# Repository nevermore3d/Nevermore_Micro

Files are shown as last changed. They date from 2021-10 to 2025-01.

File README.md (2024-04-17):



# Nevermore Activated Carbon Filters - Micro Edition

<div align="center">Nevermore Micro V5 Duo (dual fan)</div>

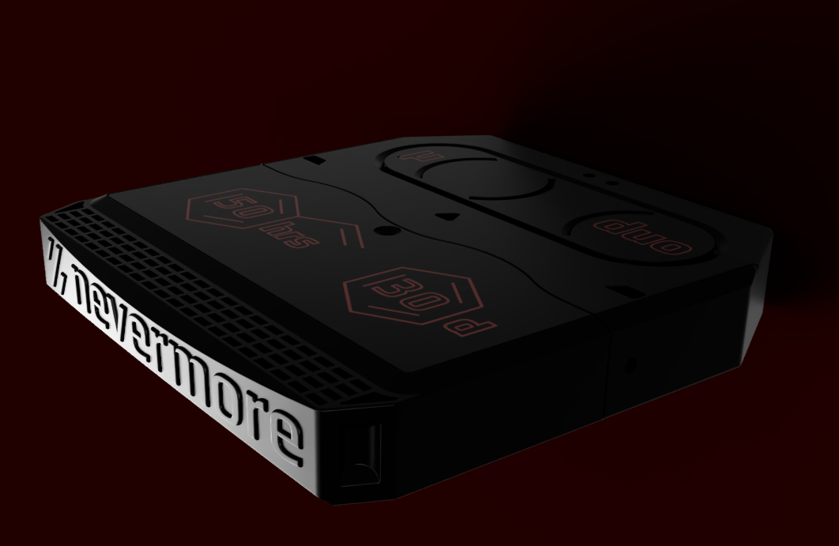
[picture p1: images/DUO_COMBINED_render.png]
Nevermore Activated Carbon Filter Micro V5 Duo


<div align="center">Nevermore Micro V4 (single fan)</div>

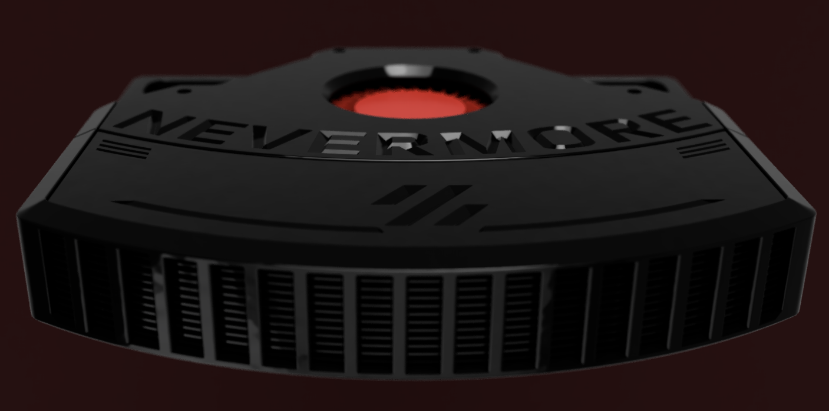
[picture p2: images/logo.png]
Nevermore Activated Carbon Filter Micro V4


Originally intended as a carbon fume filter for Voron V2, it has found its way into a multitude of other machines. Let yours be the next! Bad smells or fumes, or complaints thereof, should not keep you from being a maker!

- [Nevermore Activated Carbon Filters - Micro Edition](#nevermore-activated-carbon-filters---micro-edition)
- [About The Nevermore Micro](#about-the-nevermore-micro)
  - [Why The Nevermore?](#why-the-nevermore)
  - [Nevermore Background](#nevermore-background)
  - [Nevermore V4, First Release](#nevermore-v4-first-release)
  - [Nevermore V5 Duo](#nevermore-v5-duo)
- [FAQs](#faqs)
  - [What are differences between V4 and V5 Duo?](#what-are-differences-between-v4-and-v5-duo)
  - [Why use a single fan version, if dual is better?](#why-use-a-single-fan-version-if-dual-is-better)
  - [What other changes does V5 bring?](#what-other-changes-does-v5-bring)
  - [What fans should I use?](#what-fans-should-i-use)
  - [How do I make a suggestion/report a bug/find out more?](#how-do-i-make-a-suggestionreport-a-bugfind-out-more)
- [Getting Started](#getting-started)
  - [SOURCING THE PROPER ACID-FREE CARBON](#sourcing-the-proper-acid-free-carbon)
  - [NEVERMORE 3D PRINTER CARBON](#nevermore-3d-printer-carbon)
  - [BOM (V5)](#bom-v5)
  - [BOM (V4)](#bom-v4)
  - [Assembly](#assembly)
    - [Instructions for V5](#instructions-for-v5)
    - [Instructions for V4](#instructions-for-v4)
  - [Final Thoughts on Usage](#final-thoughts-on-usage)
- [Credits](#credits)
  - [Contributing](#contributing)
  - [License](#license)
  - [Contact](#contact)
  - [Acknowledgements](#acknowledgements)
  - [Special Thanks](#special-thanks)

# About The Nevermore Micro

[VOCs (Volatile Organic Compounds)](https://en.wikipedia.org/wiki/Volatile_organic_compound) are common in daily life but VOCs generated from 3D printing are known to cause severe health issues and even cause cancer in some cases.

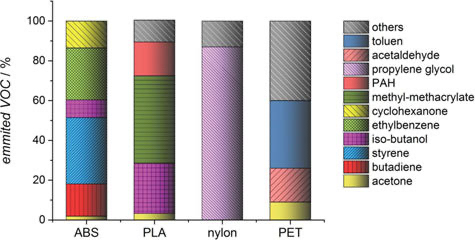
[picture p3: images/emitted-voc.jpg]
Emitted VOCs


A study from 2013 of [ultrafine particle emissions from desktop 3D printers (2013)](https://www.sciencedirect.com/science/article/pii/S1352231013005086) is a good start to understand the importance of your filament choices and the printer's environment.

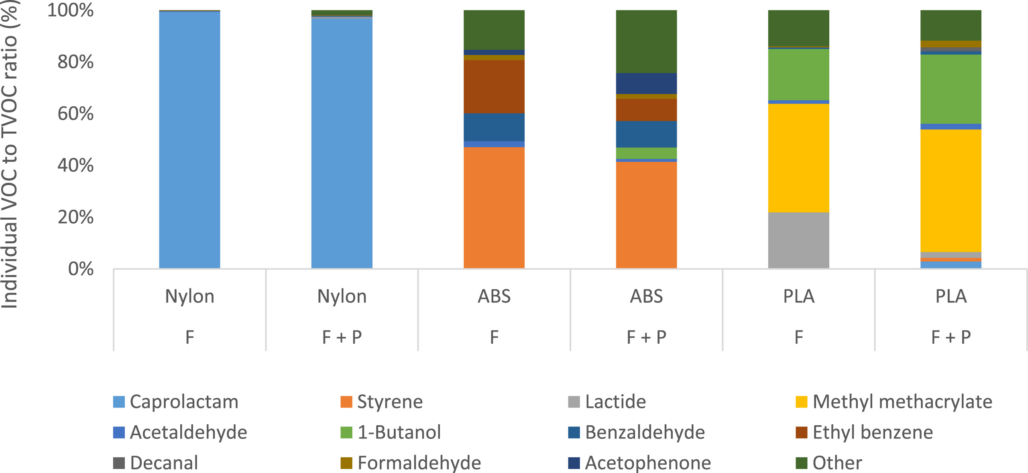
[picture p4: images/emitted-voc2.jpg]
Characterization of volatile organic compound emissions from consumer level material extrusion 3D printers (2019)

_(credit: [Characterization of volatile organic compound emissions from consumer level material extrusion 3D printers (2019)](https://www.sciencedirect.com/science/article/pii/S0360132319304196))_

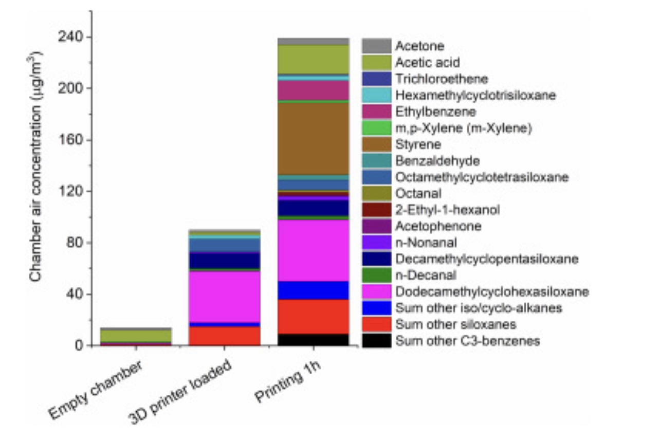
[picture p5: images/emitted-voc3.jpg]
Characterization of particulate and gaseous pollutants emitted during operation of a desktop 3D printer (2019)

_(credit: [Characterization of particulate and gaseous pollutants emitted during operation of a desktop 3D printer (2019)](https://www.sciencedirect.com/science/article/pii/S0160412018323663))_

## Why The Nevermore?

At the end of the day, a fresh single-pass filtered exhaust (at brand new) has perhaps 70% VOC removal efficiency while still exhausting 30% of the nasty. A worn-in 50% efficiency recirculation filter achieving four passes would still remove 94% of the bad stuff. Or 99% at six passes!

The number of passes you get all depends on how well you can seal your build chamber.

Some will have a hard time achieving a good chamber seal, which creates the biggest drawback of recirculation filters - _they're air flow neutral_. Meaning, as nothing pulls air into the chamber, air can diffuse freely to the outside through any remaining gaps. And that air could be _zero-per-cent_ cleaned...

If you plan on using only a Nevermore - be sure to seal your chamber as good as possible to prevent diffusing.

## Nevermore Background

There are many options for 3d printing air filters. Here’s a short list, and why I eventually settled on creating Nevermore:

**1. Home air purifiers**

**PRO:** Plug and play! High air flow (mostly). Will filter most particles a 3d printer produces.

**CON:** ABS headaches are not from particles, but Volatile Organic Compounds (VOCs), that are two orders of magnitude smaller than any particles a HEPA or ULPA could trap - they’re essentially gasses.

While home purifiers typically also contains carbon filtration and/or photocatlytic UV filtration stages, they will still not be suitable for 3d printing. Why? Efficient carbon adsorption in sufficient amount and stages is an absolute airflow killer, so most purifiers contain only a thin layer of carbon mesh/pellets that will be fully adsorbed within days or weeks at full power. And even if the filter is not used, contact with air saturates the carbon in 1-2 months. Yet they’re advertised as lasting for 6 months – that's only true for the HEPA component, not the VOC adsorbant carbon we're after.

And replacement filters typically run 20-60 USD a pop. Quite a lot for changing every few weeks when the carbon component depletes.

UV photocatalyst activity can last though; however, breakdown is slow and inefficient with voc halflives of several hours. The TiO2 layer reacting to the UV will also easily get irreversibly blocked by silicates (of which there are a lot in peoples homes, in everything from sink and bathroom sealants to plaster walls). And breakdown will many times be incomplete. Styrene passing a PCO filter might get turned to even more dangerous benzene, for instance.

**2. Carbon/HEPA filter combinations like the Zortrax M Series HEPA Filters**

Same as above. The HEPA component will keep working, but the carbon is just a few pebbles per hex. It could provide partial VOC clearance when fresh, but will quickly deplete with air flow. Then you need to replace it for 36 USD after a week of printing.

**3. Wet scrubber**

Awesome for both particles and VOCs, but its an industrial solution with any smaller home versions plagued by loud noise, water leakage and mechanical issues. It's not a solution for the masses.

**So, how about Nevermore?**

Well, the carbon in those filters mentioned above, costing a lot for little duration is actually dirt cheap. Whereas you get 20 grams for 36 USD with a zortax filter, **you can get 5000 grams for 36 USD in bulk**.

And with an enclosed chamber, you don't need the air flow of a room-size air purifier. Even a 350mm V2 Voron only holds about 5cf, meaning even a partial flow from a 5015 fan of 0.5-2cfm is enough to filter the fumes efficiently at the source.

So what are we waiting for? We got lots of cheap carbon. We can replace it easily. We don't need high airflow to clean a small chamber. We deal with poor efficiency of one-pass carbon filters by multiplying the amount and recirculate the air.

Enter, _The Nevermore_.

## Nevermore V4, First Release

Nevermore V4 is a refinement of the V3. V4 adds a air guides, as the previous versions had the majority of air flow on just one side of the filter (most recent version has all supports removed yet again!). The cartridge lid also mounts a bit sturdier, and V4 now has separate base pieces for use with Vorons other than 2.4.

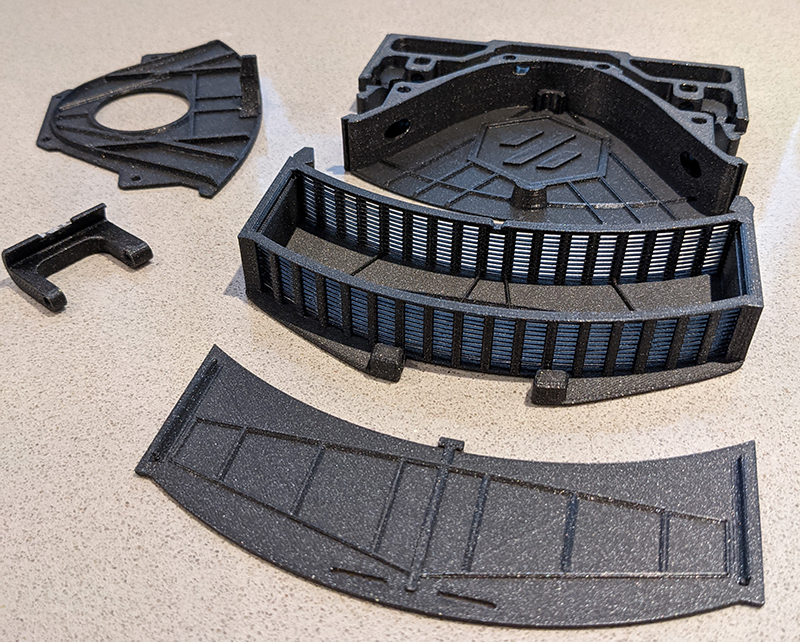
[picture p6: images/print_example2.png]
Nevermore Micro V2 Prototype


The V4 was the first official release of the Nevermore Micro to the public.

## Nevermore V5 Duo

Following the V4, the V5 Duo was released that changes the direction of air flow, better suited for when the Nevermore Micro would be placed flat on the bottom or top of the printer. Though there are other "outlet" options, like for the V1.8/Trident style that blows outwards and not up.

The V5 Duo also adds a 2nd additional 5015.

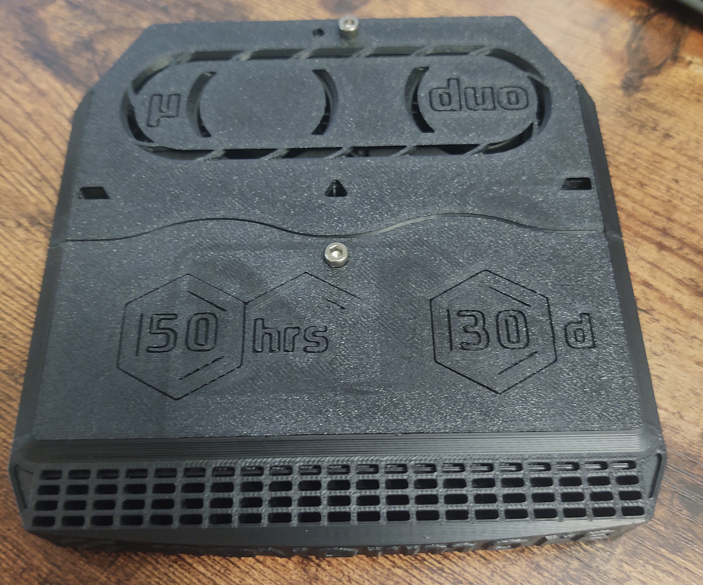
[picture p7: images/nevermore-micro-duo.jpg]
Nevermore Micro V5 Duo


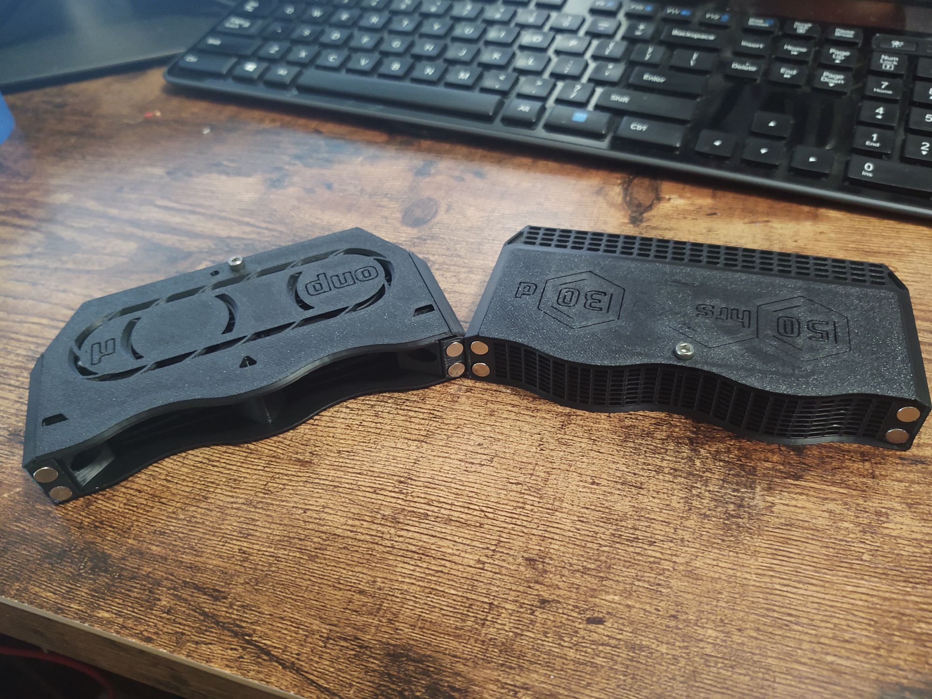
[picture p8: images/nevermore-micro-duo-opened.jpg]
Nevermore Micro V5 Duo


_(Nevermore V5 Duo. used with permission from Tightwad(JT)#6055)_

This repository hosts both versions, as they are the same in design and function.

# FAQs

## What are differences between V4 and V5 Duo?

The current NM Micro versions are V4 and V5 Duo.

V4 utilizes a single dissected 5015 fan that is glued in place to spread the airflow over the entire filter surface (something impossible to do with an intact scroll, which focuses the air too much). The intake is on the top, and exhausts out the front.

V5 Duo uses two blowers in parallel to achieve a more even spread of airflow while keeping the pressure-generating scrolls intact; however, it still needs some slight modifications to the scroll exhaust. The intake is on the top, and exhausts upwards.

## Why use a single fan version, if dual is better?

_Dual is not better._ The area per blower is halved, so what is gained in air flow is lost in increased restriction per blower. There should be some improvements though, from linear air flow and intact scroll.

Also, the V4 single fan version may be better suited for printers where the Micro has to be mounted vertically, like on the side of a Voron V0.

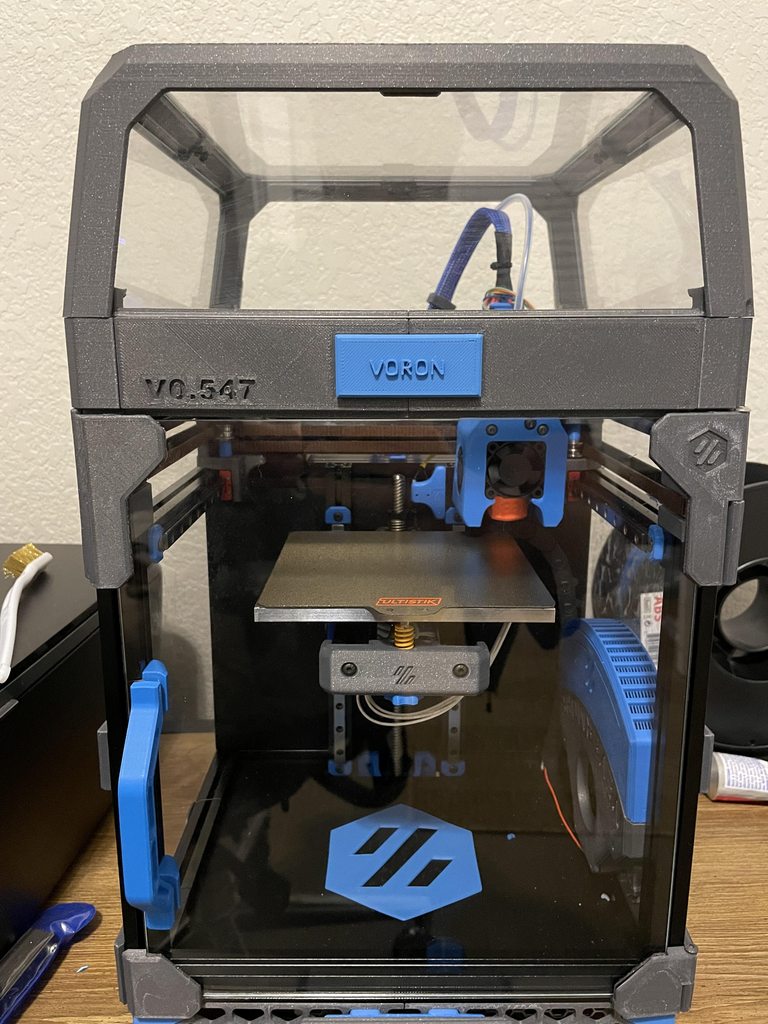
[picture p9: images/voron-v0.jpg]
Voron V0.1 with Nevermore V4


_(Voron V0.1 w/Nevermore V4. used with permission from DoubleT#0448)_

The single fan version of the V4 design in the Voron V0 above would draw the air from under the build plate, and exhaust it upwards, creating a circulation flow within the printer.

Air circulation is critical to filter as much of the VOCs within the build chamber as possible. Not only that, but it would help heat the chamber faster and achieve higher chamber temps.

However, on a Voron V2 or similar printer, the V5 Duo version would be better suited when placed under the bed as the upward exhaust venting creates a good circulation effect.



_(Voron V2 w/Nevermore V5. used with permission from Laserbeak43#2729)_

## What other changes does V5 bring?

- Exhausts air upwards
  - Better heat spread in the Voron V2 chamber
  - Less air leaks through Voron V2 split doors
- BOM 6x3 magnets are standard
- Blower fans are seated by bolts again, with less modifications needed

## What fans should I use?

Aim for any 5015 blower with a rating above 200Pa / 20mmH2O / 1 inH2O.

Since the fan (probably) cant be reused for other projects and will function in a high temp environment affecting its lifetime, go for budget. The Sunon Maglev MF50151VX (12V) / MF50152VX (24V) (high speed version, 6000 rpm) is good but unfortunately almost impossible to find as most are fakes. The GDStime 6000rpm Dual Ball bearing is another good option, but quality may vary. The Delta BFB0524HH is a gucci option, as is the special micro versions made for the papst rlf-35 which is an equally awesome and expensive fan. Any fan that works well for stealthburner should be a good option for nevermore micro as well.

See the BOM below for more details.

## How do I make a suggestion/report a bug/find out more?

- [The Nevermore Micro](https://github.com/nevermore3d/Nevermore_Micro)
  - [Report a Bug](https://github.com/nevermore3d/Nevermore_Micro/issues)
  - [Request a Feature](https://github.com/nevermore3d/Nevermore_Micro/issues)
- [Explore all Nevermore Activated Carbon Filters](https://github.com/nevermore3d)

# Getting Started

You're ready to build a Nevermore Micro? Cool!

> [!NOTE]  
> MADE FOR ABS/PC/PETG - USE A DECENTLY HEAT RESISTANT FILAMENT !!

> [!NOTE]  
>  Since you are committing to fan dissection, be aware a 5015 used for a NM Micro will most likely never find a different purpose!

## SOURCING THE PROPER ACID-FREE CARBON

**IMPORTANT!** Since first release the varying quality carbon out there has become increasingly evident. Users has both gotten bad carbon as well as outright dangerous stuff (in one case oxidizing most metal surfaces in a new voron in minutes. Be sure to vet your carbon supplier! You do not want your printer to look like this.

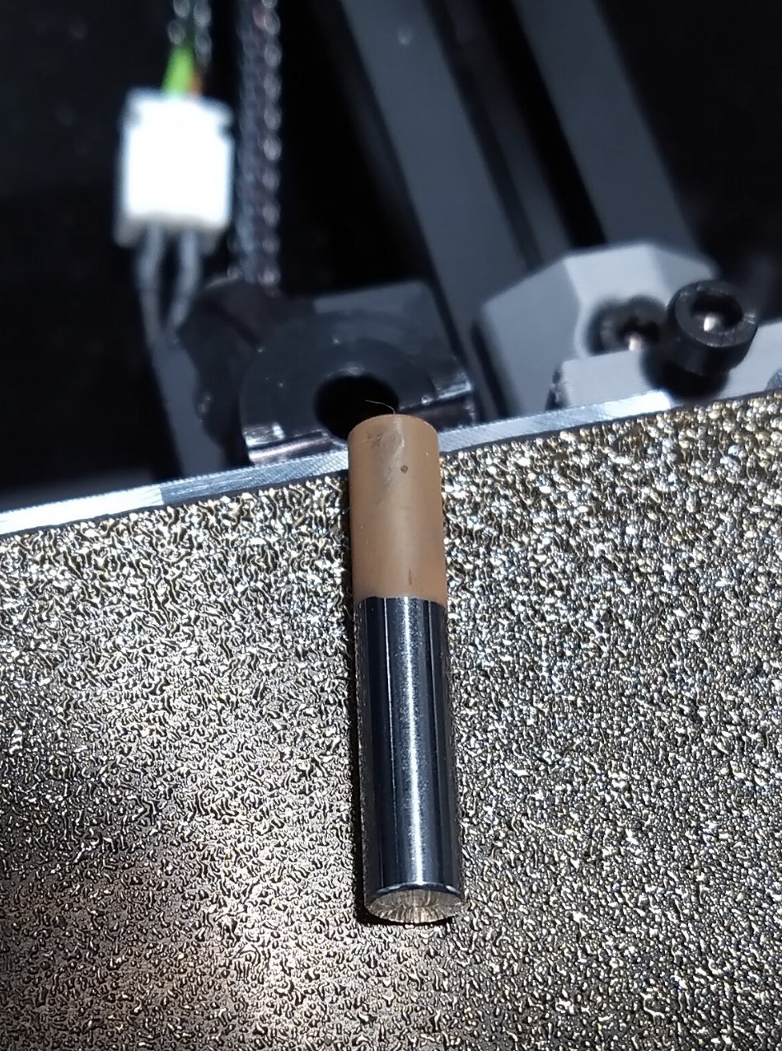
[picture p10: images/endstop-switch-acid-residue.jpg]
Acid residue on end-stop switch oxidizing


_(z end-stop switch after using acid residue carbon for 30 minutes, oxidizing)_

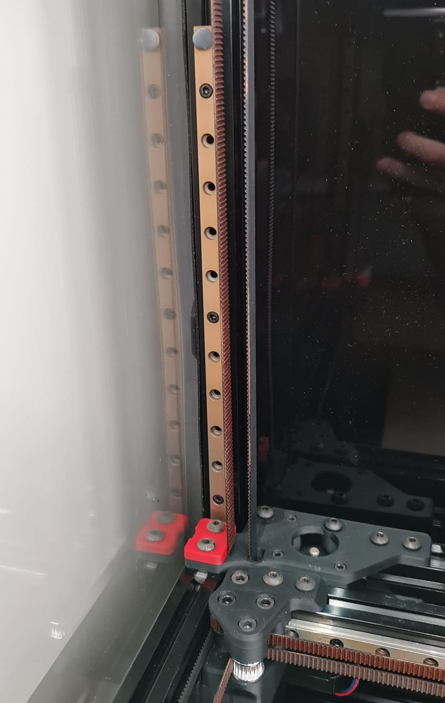
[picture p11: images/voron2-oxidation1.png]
Acid residue on rails and screws oxidizing


_(oxidation on rails and screws after using acid residue carbon. used with permission from Zeptron#8880)_

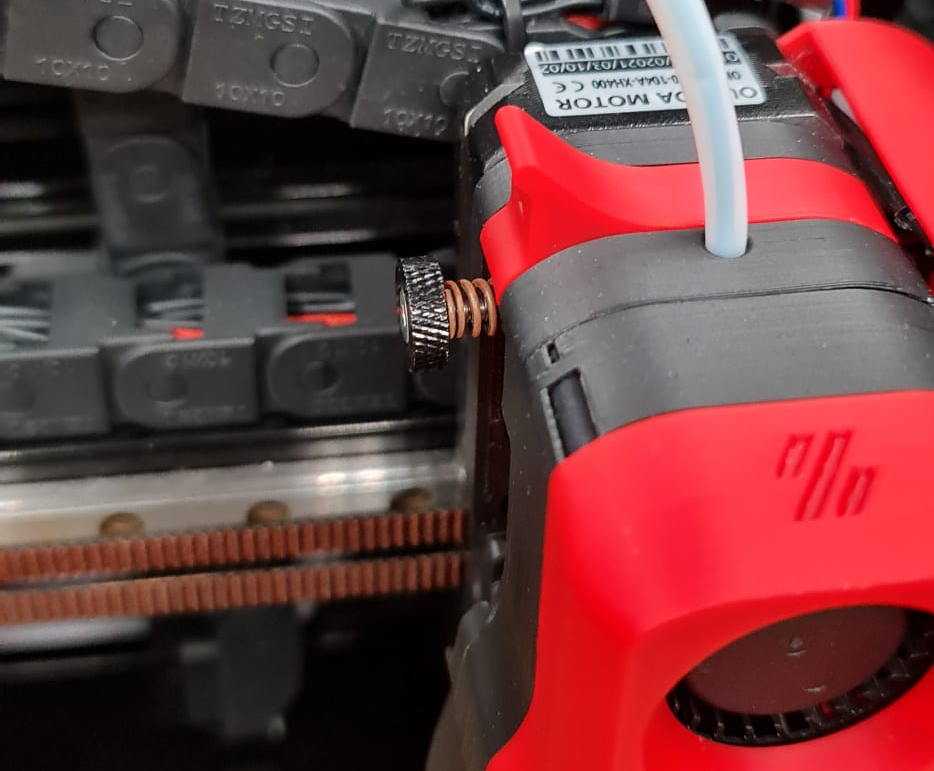
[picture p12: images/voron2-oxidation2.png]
Acid residue on filament tension spring oxidizing


_(oxidation on filament tension spring after using acid residue carbon. used with permission from Zeptron#8880)_

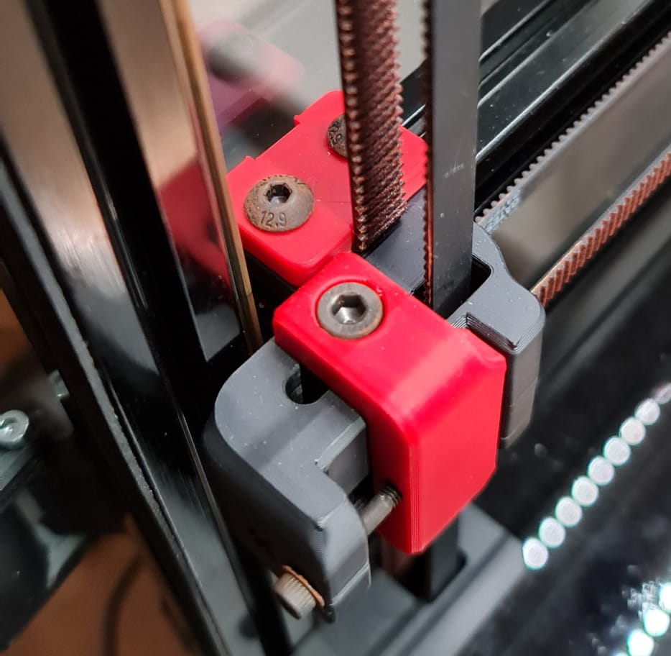
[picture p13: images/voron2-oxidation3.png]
Acid residue on bolts and washers oxidizing


_(oxidation on bolts and washers after using acid residue carbon. used with permission from Zeptron#8880)_

**Picking the Right Carbon for Your 3D Printer**

Choosing the optimal activated carbon for a specific task requires careful
consideration of several key factors, including surface area, CTC/benzene
efficiency, porosity, and pH. These properties play a crucial role in determining the
effectiveness and efficiency of the activated carbon in adsorbing target
contaminants!

**Surface area** is perhaps the most critical factor, as it directly influences the
adsorption capacity of the activated carbon. A higher surface area allows for more
adsorption sites, enabling the activated carbon to capture and retain a greater
amount of contaminants. Activated carbons typically range from 500 to 1250 m²/g,
and a carbon of 1200 m²/g would have twice the capture capacity compared to a
600 m²/g carbon. A good carbon usually has at least 1000 m²/g.
Be sure you're not getting scammed by buying 25% cheaper carbon that lasts half
as long!

**CTC** (Carbon Tetrachloride) **efficiency** - or even better for 3D printing applications,
aromatic hydrocarbon efficiency - is another important consideration, as it
measures the activated carbon's ability to adsorb volatile organic compounds
created from 3D printing. A higher CTC efficiency indicates a greater proportion of
micro-pores, which are essential for capturing - and holding on to - small
contaminants like airstream VOCs. Choosing an activated carbon with a CTC
efficiency that matches the size of the target contaminants ensures optimal
adsorption performance. A good carbon usually has at least 60% CTC.
Be sure you're not getting scammed by buying 25% cheaper carbon that captures
half as much!

**Porosity** , which refers to the distribution of pore sizes within the activated carbon,
also plays a significant role. Activated carbons, depending on quality and carbon
source, will have different ratios of micro-pores (<2 nm), meso-pores (2-50 nm),
and macro-pores (>50 nm). For general use, an even mix might be preferred, as
they can effectively capture a broad spectrum of contaminants while allowing for
efficient mass transfer and regeneration. However, for 3D printing use, a high
micro- and mesoporosity is ideal to both capture VOCs (<2 nm) and VOC-
agglomerates (ultra-fine particles, <50 nm), whereas macropores will struggle to
hold on to VOCs in a hot application like a 3D printer's heated chamber. Good
carbon types for our application are usually sourced from coconut or anthracite, as
they are highly microporous, whereas other common carbons, such as bamboo or
bituminous, usually have a larger percentage of macropores.
Be sure you're not getting scammed by buying 25% cheaper carbon that releases
half the VOCs again!

**The pH of your activated carbon** should be considered, especially when dealing
with pH-sensitive applications or contaminants. Activated carbons with a neutral or

slightly alkaline pH are suitable for most applications, while acidic or basic activated
carbons may be required for specific tasks. In order to capture any VOC type
generated from any filament, a neutral carbon (capable of binding to both neutral,
acidic, and alkaline VOCs) is preferred. Some users have also experienced severe
printer corrosion from using acid-contaminated/treated carbon that, for some
reason, got released with the heating cycles.
Be sure to buy a 3D printer-safe carbon that is steam-activated and not acid-
treated/coated!

**Compare carbons in a jiffy**

As a general comparison number for neutral carbons, try multiplying surface area
and CTC efficiency (available space * capturing efficiency):

**Carbon A** : 1250 m²/g * 80% CTC would be 1250 * 0.8 = 1000 ( _yes, this is
Nevermore specs_ )

**Carbon B** : 1000 m²/g * 50% CTC would be 1000 * 0.5 = 500

This means that Carbon A can be expected to be 2x the performance, capturing
more VOCs for longer.

Be sure to buy Carbon A unless it's twice the price (or if you wish to refill your
cartridges twice as often - it gets tedious quickly!).

## NEVERMORE 3D PRINTER CARBON
**Nevermore offers its own premium carbon of unmatched specifications through selected voron resellers.** Its the best activated carbon for 3D printer use we have found after speaking to most major, vetted suppliers, offering benzene adsorbtion of up to 48 wt%, **surface area of 1250** and **CTC value of 80**. It doesn't come cheap compared to bulk carbon from amazon, but its safe, has unbeatable performance, and every purchase supports the nevermore project by at least a dollar.  

[All Nevermore resellers here](https://github.com/nevermore3d/Reseller)

## BOM (V5)

- 2x 5015 blowers (rating above 200Pa / 20mmH2O / 1 inH2O)
  - Sunon Maglev MF5015VX (high speed version, 6000 rpm. NOTE: There are A LOT of fake sunons out there, even from usually reputable sources. Blantant examples include 24V versions. Also, Sunon does not officially reecommend PWM:ing this fan, so while its still perfectly doable it can have unintended consequences later on) (There is no 24V version for this fan only comes in 12 V)
  - GDStime 6000rpm Dual Ball bearing on Aliexpress (This is 12V rated fans)
  - Delta BFB0524HH (This is 24V rated fans)
  - Avoid mechatronics fans for this purpose.
- 6x M3, 5 mm OD, 4 mm height heatset inserts (standard voron issue)
  - 1 in plenum base to secure plenum lid
  - 1 in cartridge base to secure cartridge lide
  - 4 in fans (2 in each fan × 2 fans)
- 8x ⌀6x3 mm round magnets
- 1x 2 pin JST header
- 4x M3x16 BHCS
  - for heat inserts that go into the four fan tabs
- 1x M3x18 BHCS
  - ONLY for delta and v1.8 variants
- 1x M3x6 BHCS
- 1x M3x4 BHCS
  - for the extra hole in the plenum@lid for symmetry (it doesn’t attach to anything and is totally optional)

Acid-free Activated Carbon

- 4mm Active Carbon Air Filter Pellets

Optional for the cartridge closure

- 1x M3x0.5mm Heatset inserts
- 1x M3x6 BHCS

Optional for Vorons or any printer with 2020 extrusions

- 2x M3x12 SHCS
- 2x M3 2020 T-Nuts

Optional for Vorons or any printer using 24PSU
- 24 to 12 buck converter

## BOM (V4)

- 1x 5015 blowers (rating above 200Pa / 20mmH2O / 1 inH2O)
  - Sunon Maglev MF5015VX (high speed version, 6000 rpm. The 5000 rpm might be okay also)
  - or, the $4-6 GDStime 6000rpm Dual Ball bearing on Aliexpress
- 4x M3, 5mm OD, 4mm height Heatset inserts (standard voron issue)
  - 2 for seating plenum to base
  - 2 for seating plenum lid to plenum
- 8x ⌀4x6 mm or ⌀6x3 mm magnets
  - Make sure to print correct parts (4x6 or 6x3 files)
- 1x 2 pin JST header
- 2x M3x10 SHCS
  - for seating plenum to base
- 2x M3x6 BHCS (any size, fits up to 20mm)
  - for seating plenum lid to plenum

Acid-free Activated Carbon

- 4mm Active Carbon Air Filter Pellets

Optional for Vorons or any printer with 2020 extrusions

- 2x M3x12 SHCS
- 2x M3 2020 T-Nuts

## Assembly

Check out assembly images (**take note at how the fans are cut!**) here: [Nevermore V5 Plenum Assembly Album](https://ibb.co/album/0BN405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)

### Instructions for V5

Print pieces without supports. This goes for all Nevermore parts. Do note that there as **built-in support** below the cartridge insert. This is meant to be easily removed by pushing or crushing (it's a single line wall). 

### Instructions for V4

Start by cutting up the 5015 so just the center remains. Take off the top half, cut the bottom piece circular along the fan blades. We aim for removing the focused air stream and instead achieve an even pressure across all of the filter medium.

The Nevermore Micro has three main parts: **Base**, **Plenum**, and **Cartridge** (plus lids for the plenum/cartridge).

- **Base** is mounted in the 130mm space between the bottom extrusions found on many vorons (designed for v2 originally). It’s seated with one m3 on each side, that screws into to a receiving 2020 M3 T-nut.

- **Plenum** holds the cut up 5015 fan, and is seated with two m3 screws into the base (base has two recieving m3 4mm heat inserts) on each side.

- **Cartridge** holds the filter medium of your choice (made for 4mm air filter active carbon pellets, but feel free to filter with what you think works best!). It snaps onto the Plenum piece for easy and quick removal.

For wiring, you are free to connect however works with your printer. If you do not have any direct controls on your MCU (controller board), then directly wiring may be your only option (with an inline switch).

However, if your MCU does have an additional fan output, then it is recommended to connect to it. If you are using Klipper on a Raspberry Pi, you have the option of using PWM fans and connecting the control wire to one of your PWM outputs on the RPi 40-pin header.

## Final Thoughts on Usage

**PID tune AGAIN if a Nevermore Micro is installed right beneath a heated bed, or draws/exhausts air over the bed thermistor. This is important, as worst case it could cause the bed to overheat, and/or make the heater adhesive burn (this will smell worse than any ABS printing!), and/or possibly even damage the bed heater.**

The Nevermore Micro's activated carbon will not filter Ultra-Fine Particulates (UFP). This is what the HEPA filter does in the Nevermore Mini (not released yet) and [Nevermore Max](https://github.com/nevermore3d/Nevermore_Max) variants. Those also have built-in negative-pressure fans.

However, you can achieve the same results with the Nevermore Micro by using a HEPA filter of your own and creating slightly negative air-pressure within your build chamber, exhausting air outwards at a slow pace. Since you are filtering with the Nevermore, the vast majority of VOCs will be filters by the active carbon filtration, leaving the HEPA filter to capture the remaining UFPs. This also greatly extends the live of your HEPA filter as the Nevermore Micro will be accumulating the larger particulates.

To create a negative pressure within your build chamber, simply install a fan to slowly draw air out of your build chamber and our through a HEPA filter. Voron machines already have such a design with their rear exhaust housing for HEPA filters.

The negative pressure will also eliminate diffusion, especially if your build chamber is not completely sealed.

# Credits

The Nevermore Activated Carbon Filter was modelled in [Fusion 360](http://autodesk.com).

## Contributing

Please contribute! I'd like to incorporate VOC sensors, making the filter smart (running on low-noise mode at an acceptable VOC level, then ramp up at the end to clean more thoroughly before doors open).

## License

Distributed under GNU General Public License version 3.0 (GPLv3)

## Contact

- Discord: 0ndsk4 - (<https://discord.com/user/0ndsk4>)
- Nevermore: [https://github.com/nevermore3d](https://github.com/nevermore3d)

## Acknowledgements

- [The Voron Dev Team](https://vorondesign.com/)

## Special Thanks

- [eduncan911#4852](https://github.com/eduncan911) as the Git Guru to publish all of this

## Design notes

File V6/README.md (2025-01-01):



# Nevermore Micro V6

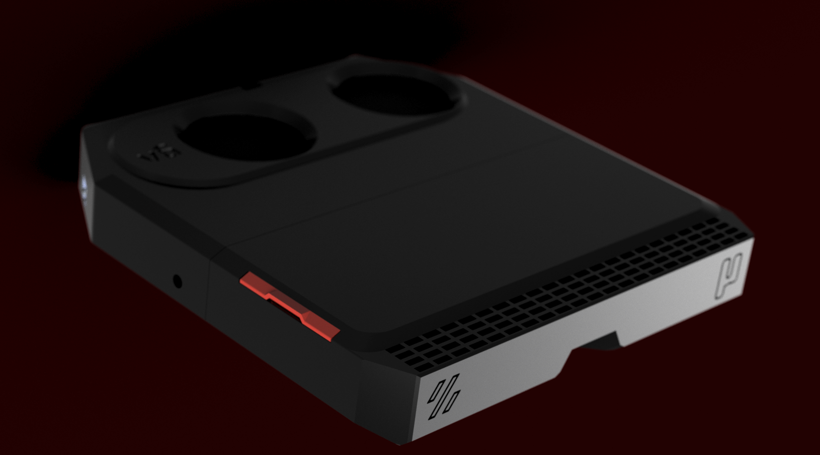
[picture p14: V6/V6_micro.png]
Nevermore Micro V6


Nevermore Micro V6 is here! It is designed to supersede both the V4 and V5 duos, which will soon be considered legacy designs.

## What's New?

- **Intact 5015 Fans:** V6 now make use of fully intact 5015 fans, eliminating the need to cut the fan scroll or wires. This raises a concern: does it waste carbon if airflow from a small 15mm 5015 fan exhaust isn't spread over the entire 130mm filter surface? Yes, usually - however, we have overcome this challenge through use of evasees and vanes to efficiently spread the airflow within the small plenum space. This means all the carbon receives airflow immediately, without requiring any fan modifications.

- **Enhanced Heat Tolerance:** Unlike its predecessors, V6 can tolerate higher levels of heat. The V4 and V5 had thinner lids that could bend or warp, especially when subjected to temperatures above 100°C under a heated bed. This sometimes resulted in broken or damaged units. However, the V6 is beefed up to address this issue. With a thicker frame, structured vanes, and lids strategically placed away from the heat source, the chances of melting a Nevermore Micro are significantly reduced.

- **Improved Airflow:** V6 boasts superior airflow. We have achieved this by optimizing the printing direction, which allows for built-in seals. Say goodbye to air leaks between the cartridge and the plenum! Furthermore, the air intakes have been redesigned to accommodate increased airflow. Now, it can process the chamber volume of a 250 Voron in just 30 seconds, and a larger 350 in approximately 2 minutes.

- **Reduced Noise:** V6 generates less noise compared to the V5, thanks to a redesigned air intake.

- **Compatibility:** V6 can be printed on any machine, including on a Voron v0 on which a v5 duo previously wouldnt fit. Yet the size is the same, its dark sorcery.

- **Sleek Design:** V6 not only performs exceptionally but also looks awesome. It features a novel jalousie lid design with no bolts, allowing for convenient one-handed carbon swaps. Gone are the days of dealing with annoying bolts or latches when swapping carbon. Rest assured, this design remains super secure. You have to try it to believe it! Jalousie demo [here](https://youtube.com/shorts/sSmVfhcDKrI?feature=share).

## Print material and settings
- Designed and prototyped with ABS materials. Any material that is heat resistant enough for the installation spot will likely work, but brittle material (i.e regular PLA) should be avoided for the jalousie slider and the spring fan fasteners.
- Made for standard voron settings. 0.2 mm layer height needed for supports to line up right, and 0.4-0.5mm line width for optimal mesh printing. 5 walls recommended for jalousie structural integrity, otherwise its pretty sturdy regardless.
- **JALOUSIE** can be break if your slicer settings interferes with the intended extrusion path. A suggestion from @Haldamir is to print it with 0 bottom solid, 1 top solid layers, 5 perimeters and 0.4 extrusion width. Also 90 degrees infill angle, so the 3rd layer is printed in this orientation.
**Avoid** bottom horizontal expansion so that there are no large gaps between the parallell length-wise extrusion lines (built in gaps in the bottom and second layer forces the slicer to print in a length-wise paralell pattern. Ideally, you want these gaps to fuse slightly for greatest strength).
  Some users has reported going **slow** for the first three layers improves the structural rigidity, as it gives more time for the layers to fully fuse. If your jalousie is prone to crack, try slowing down to 40mm/s and perhaps raise the **temp** slightly for better fusing. There is also a "thin" jalousie that might be a better fit for stiffer materials. It has bend layers that are 0.4mm instead of 0.6mm, which paradoxically will make a jalousie prone to cracking with _bending_ hold up better.

## BOM and Installation

### BOM
- 2x 5015 blowers (compatible with Delta, Honeybadger, Gdstime, and Winsin. Sunons might fit but the intake holes may not line up perfectly). It is recommended to use blowers with good static pressure (>150Pa).
- Wiring Options
  - Single JST-XH 2-pin
    - 1x JST-XH 2-pin
  - Triple JST-XH 2-pin
    - 3x JST-XH 2-pin
  - Dual WAGO 221 2-pin connectors
    - 2x WAGO 221 2-pin connectors
- 8x 6mm wide and 3mm deep magnets
- Mounting Options
  - Back Extrusion Mounting
    - 2x M3x4x5 heat inserts
    - 1x extrusion T-nut
    - 2x M3x6mm SHCS
  - Bed Extrusion Mounting
    - 1x M3x4x5 heat inserts
    - 2x Extrusion T-nut
    - 1x m3x16 SHCS
    - 1x m3x20 SHCS
### Support Removal

Before installation, there are a few support pieces that need to be removed:

**Plenum:**
- A long bridge along the top of the cartridge.
- The two triangular pillars extending to the fan tab slot from the area around the fan intakes.
- The top portion of the two fan intakes.
- On the bottom right evasee/side bolt mount slot as viewed from the front.

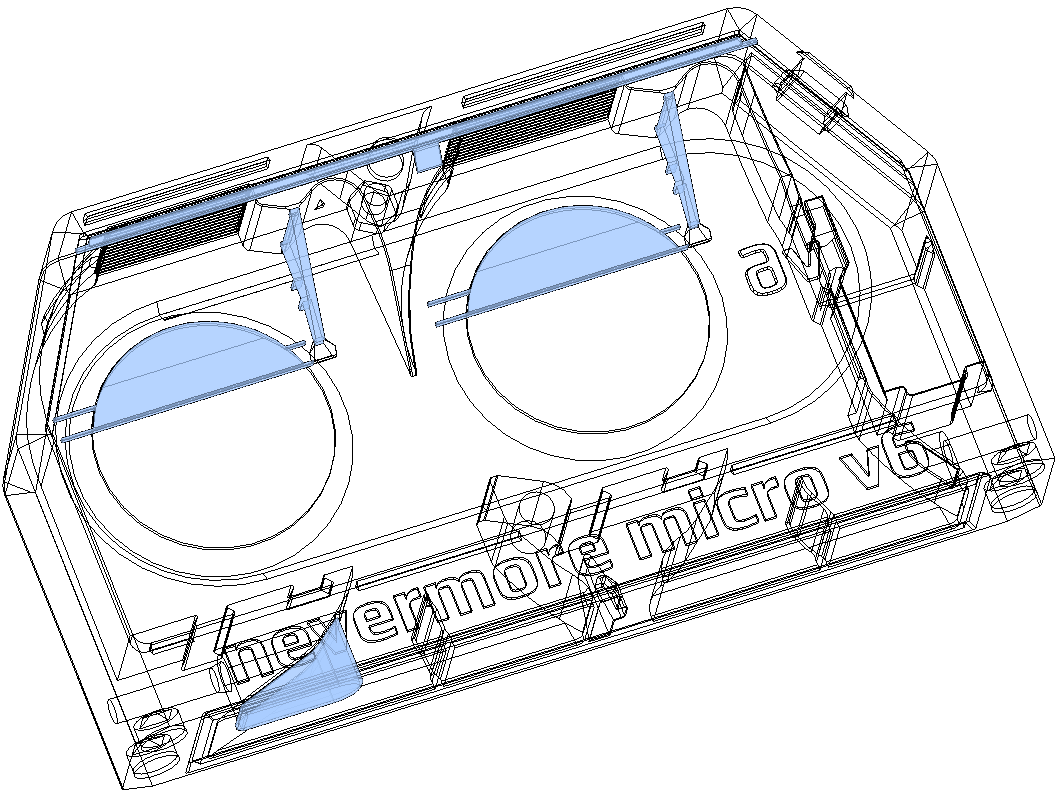
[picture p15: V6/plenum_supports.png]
Plenum Supports


**Cartridge:**
- The lid/jalousie area has a single support piece. Be cautious when removing it, ensuring not to damage the jalousie sliding path. If the support is fused, use an X-Acto knife if necessary.

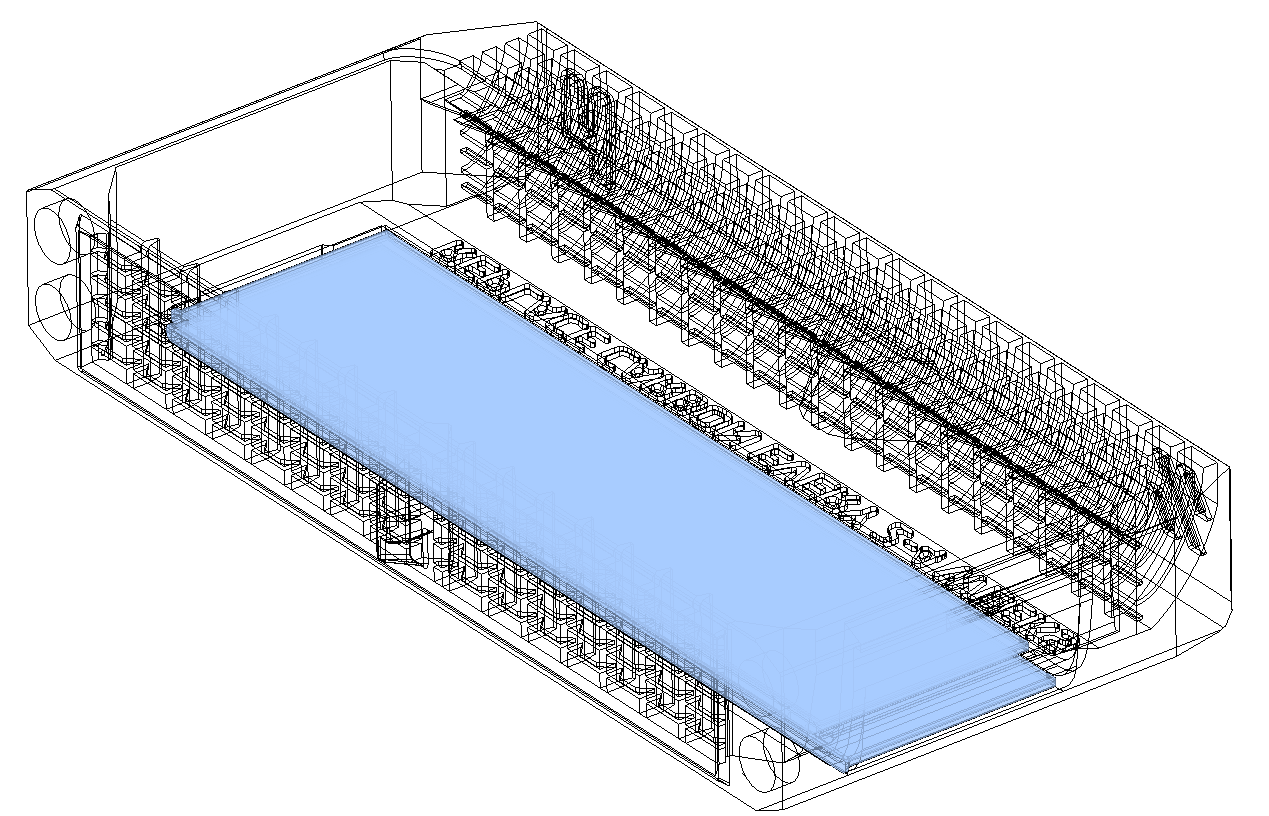
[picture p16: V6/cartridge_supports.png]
Cartridge Supports


### Plenum

#### Electronics

**Required:**
- 2x 5015 blowers (compatible with Delta, Honeybadger, Gdstime, and Winsin. Sunons might fit but the intake holes may not line up perfectly). It is recommended to use blowers with good static pressure (>150Pa).

**Wiring Options:**
1. **Single JST-XH 2-pin**: Solder both fan wires to a single JST-XH 2-pin connector and connect it to the plenum port.
2. **Triple JST-XH 2-pin**: Print the [2xJST_Holder.stl] insert to create a triple JST-XH 2-pin port. Connect the fans without cutting fan wires by daisy-chaining the 2 extra JST connectors to the plenum JST port. Note that for thicker and longer fan wires (like Gdstime), the wiring space may need to be completely filled with wire.
3. **Dual WAGO 221 2-pin connectors**: Cut the fan wires, twist the fan wires together (12V bundle + GND bundle), and use WAGO connectors (One WAGO for 12v bundle, and another WAGO for GND bundle) as wire extensions. Print the [Wire_connector.stl] that fits the plenum JST port. Insert the power wire from your printer and connect it to the corresponding WAGO socket. Lastly, insert the WAGO connectors into their slots.

**TRIPLE-JST and WAGO**

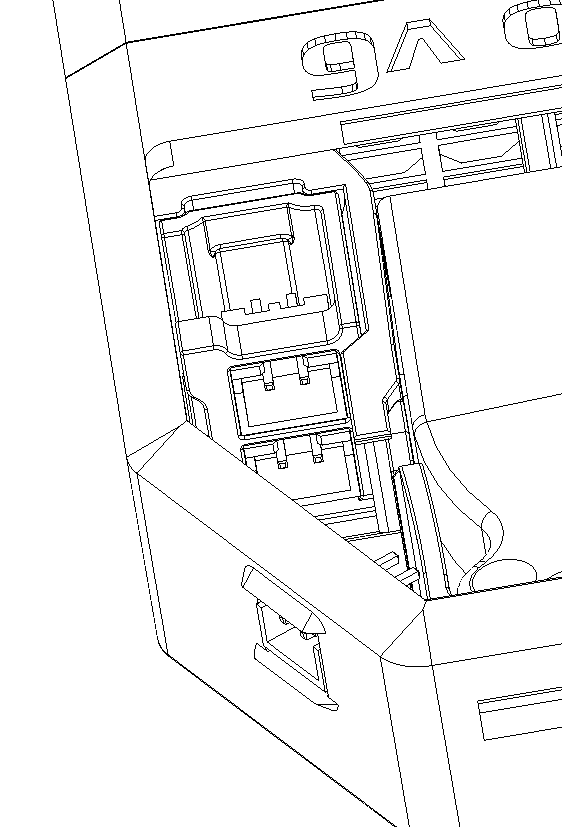
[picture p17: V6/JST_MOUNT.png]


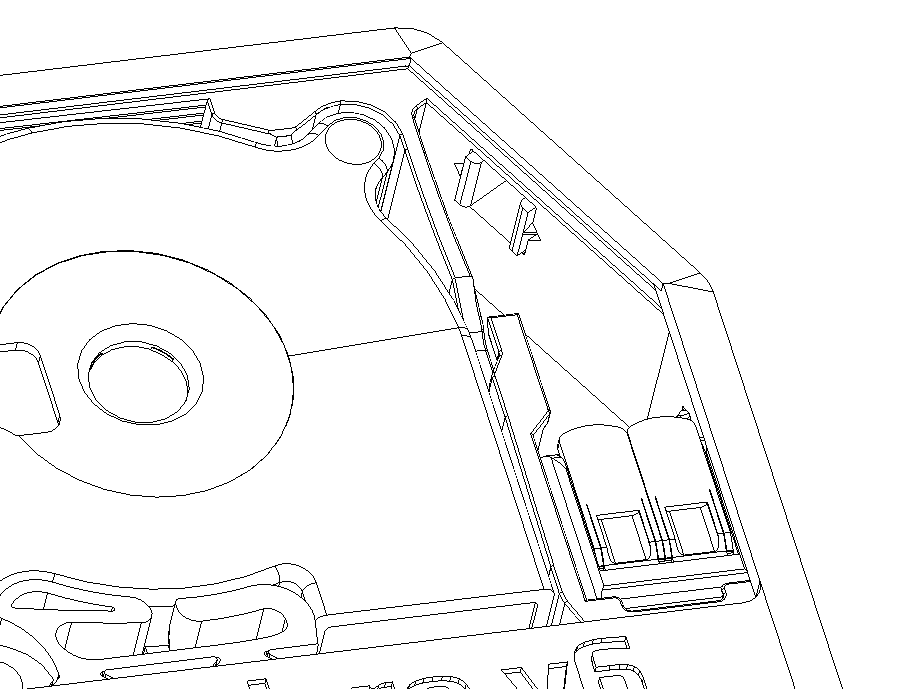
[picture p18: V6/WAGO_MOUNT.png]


#### Magnets

**Required:**
- 4x 6mm wide and 3mm deep magnets (also 4x magnets on the cartridge side, totaling 8 magnets).
**Note:** Take care when installing the magnets. A common issue is getting polarity wrong.

### Plenum Wiring and Lid Install

Plenum_Install
Plenum_Install

#### Back Extrusion Mounting

For the V0 1515 version or Trident 2020 version:
- Insert 2x M3x4x5 heat inserts, one in the back slot after lid installation, and one to secure the lid fully after snap fitting it.
- Use an extrusion T-nut.
- Seat [2020_Frame_Connector.stl] _OR_ [1515_Frame_Connector.stl] into the extrusion T-nut with an M3x6mm SHCS.
- Slide the plenum over the extrusion connector and connect the pieces with one M3x16 SHCS from the front side of the plenum.

#### Bed Extrusion Mounting

For the V2 2020 version (or sometimes the Trident 2020 bracket):
- Insert 1x M3x4x5 heat inserts, to secure the lid fully after snap fitting it (or both inserts as per above if you plan on using one back, and one side mount)
- 2x extrusion T-nuts.
- 1x m3x16 SHCS (left side mount when viewed from top/exhaust)
- 1x m3x20 SHCS (right side mount when viewed from top/exhaust)
- Bolt the V6 to an extrusion t-nut on both side of the filter when mounting under the bed on a v2. 
**Note:** Bed doesnt have to be removed; connect the wires and bolt the plenum at the front of the bed, then loosen the bolts by half a turn allowing you to slide it in to position. Once in the right position, tighten it gently with a ball type driver.

### Cartridge

#### Magnets

**Required:**
- 4x 6mm wide and 3mm deep magnets (also 4x magnets on the plenum side, totaling 8 magnets).

#### Jalousie Sliding Lid Installation

The jalousie slider can be printed in any non-brittle yet rigid material. ABS, ABS+, Nylons, PETG, and Tough PLA are suitable options. However, avoid using brittle PLA or TPU.

For the first installation, **heat the jalousie slider slightly** (for instance, by placing it on the 3D printer's heated bed just below the glass transition temperature for a minute or two). Then, insert it from the top, ensuring the matching orientation, and push it in a few millimeters at a time. The critical moment is the first bend on the first insert, so **provide support and help it bend on the opposite side of insertion to prevent cracking or damaging the sliding path**. Once inserted, slide it in and out a few times to smooth out any surface imperfections that may hinder smooth operation. Lubrication should not be necessary but can be an option if desired.

## Support My Work

If you find my work helpful, consider [buying me some filament 🖍️](https://www.buymeacoffee.com/nevermore3d).
## For more information and documentation, visit our [GitHub page](https://github.com/nevermore3d).

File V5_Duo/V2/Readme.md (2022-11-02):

Four parts; Plenum+Lid, and Cartridge+Lid.

Choose between regular and XL cartridge. XL is just 10mm longer, which can make a big difference in air flow.

Choose XL for max carbon content and filter duration, and if you don't mind the fan (200Pa+) has to run faster/noisier. You probably have to use pellets instead of granular carbon too.

Choose regular if you have granular carbon and/or a weaker fan, and/or wish to have a more silent experience. Regular also allows for somewhat higher airflow, which could make a small difference compared to XL in chamber heat up times.

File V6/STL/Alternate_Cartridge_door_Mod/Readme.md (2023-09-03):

The intent of this mod was to provide an alternative door for the cartridge other than the Jalousie which can be tricky to get right.

This model uses an M3x6 Countersunk screw with a brass insert

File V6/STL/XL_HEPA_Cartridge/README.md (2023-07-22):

# Nevermore Micro - XL?!
This cartridge is double the thickness of a regular cartridge, and wont fit under a voron v2 bed. It does however fit along a panel on any machine with at least 42 mm of space between the panel and bed. The extra height allows the installation of a Xiaomi Mijia G1 [HEPA filter](https://s.click.aliexpress.com/e/_EGPsFBt) (same as on Nevermore Stealthmax), of the size 130x40x8mm.
<div align="center">Nevermore Micro V6 XL HEPA</div>

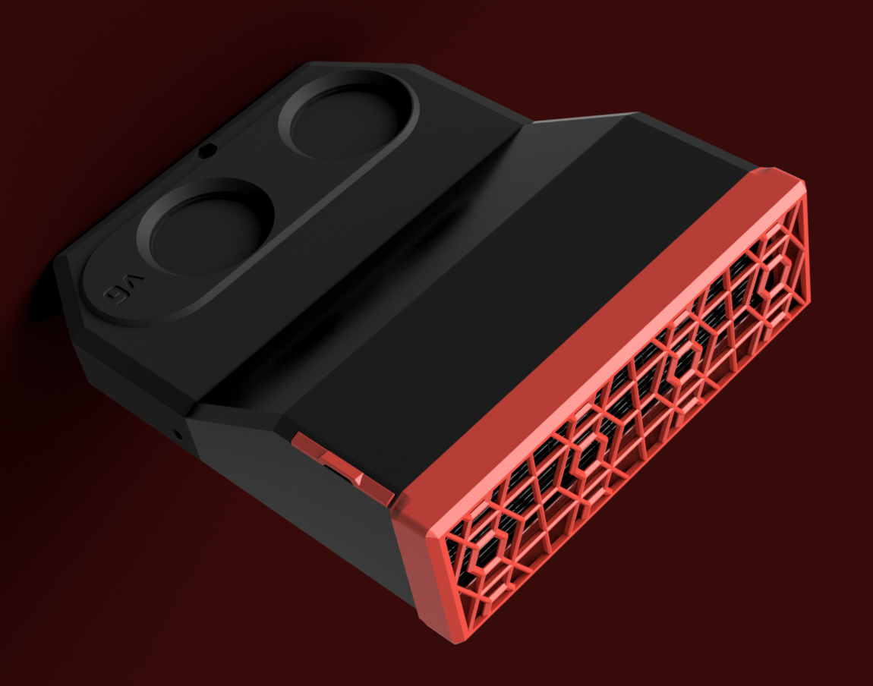
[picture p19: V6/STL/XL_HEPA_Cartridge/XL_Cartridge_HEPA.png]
Nevermore Activated Carbon Filter Micro V5 Duo Nevermore Activated Carbon Filter Micro V6


<div align="center">Nevermore Micro V6 XL HEPA</div>

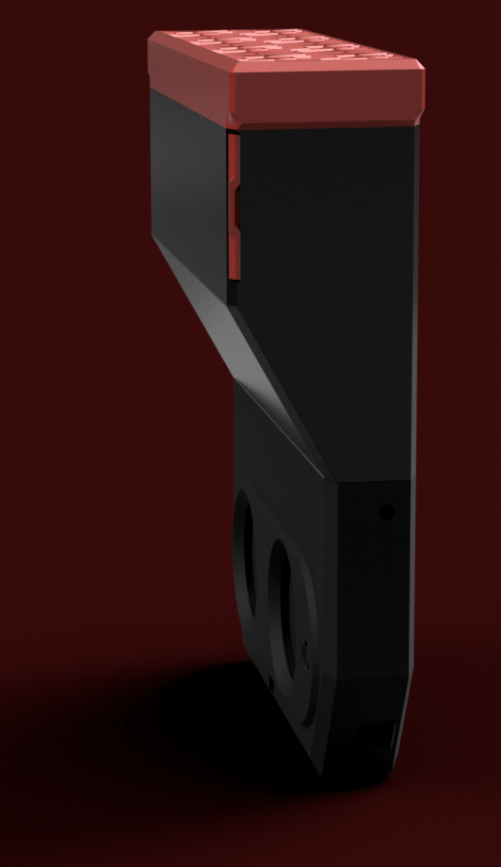
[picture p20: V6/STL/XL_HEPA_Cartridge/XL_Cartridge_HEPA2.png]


<div align="center">Nevermore Micro V6 XL HEPA</div>

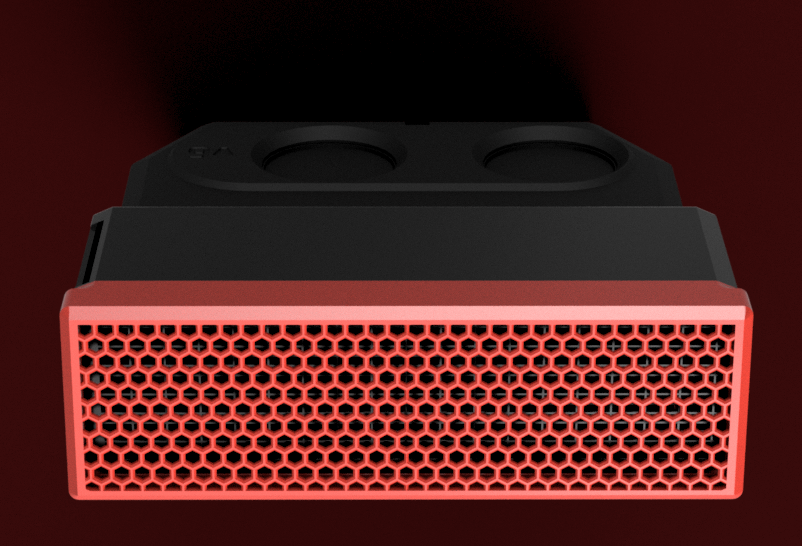
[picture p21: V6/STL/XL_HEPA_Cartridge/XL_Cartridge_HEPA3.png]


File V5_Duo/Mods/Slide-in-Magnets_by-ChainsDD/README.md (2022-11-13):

# Nevermore V5 Duo w/ Slide-in Magnets

I got tired of my magnets falling out, even after I had glued them, So I cooked up this mod.

After printing, just slide your magnets in from the top. Push the first magnet all the way to the bottom, and the second until you feel it slip into it's pocket. There's a whole on the bottom of the parts in case you need to remove the magnets.

There's two versions of the plenum, one with and one without a Wago mount on the back side. Use two 221-413 wagos for simpler, solder free wiring.

The cartrige uses the normal lids that can be found in the v2 folder. The plenum has a modified lid, so use the one here.

For extra cool points, print both lids with a color swap at about the 4th layer.

Regarding the two cartridges:
>Choose between regular and XL cartridge. XL is just 10mm longer, which can make a big difference in air flow.
>
>Choose XL for max carbon content and filter duration, and if you dont mind the fan (200Pa+) has to run faster/noisier. You probably have to use pellets instead of granular carbon too.
>
>Choose regular if you have granular carbon and/or a wekaer fan, and/or wish to have a more silent experience. Regular also allows for somewhat higher airflow, which could make a small difference compared to XL in chamber heat up times.

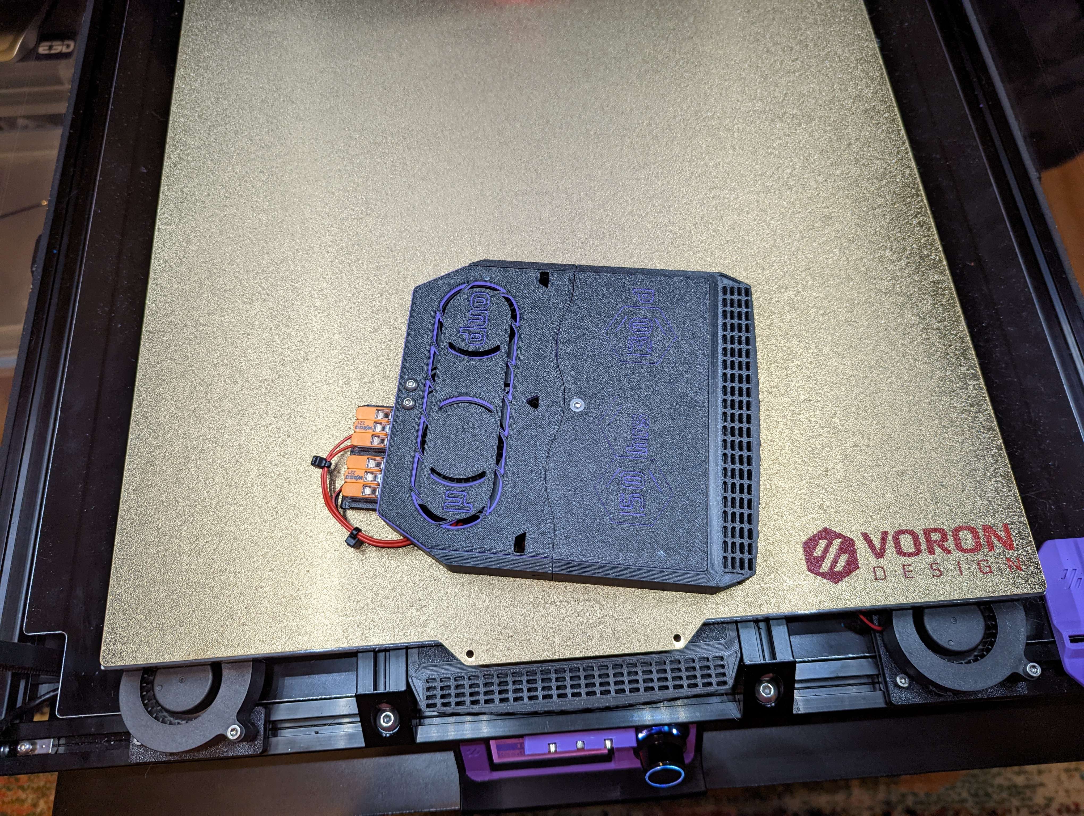
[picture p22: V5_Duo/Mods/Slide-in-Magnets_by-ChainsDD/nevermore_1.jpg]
Assembled

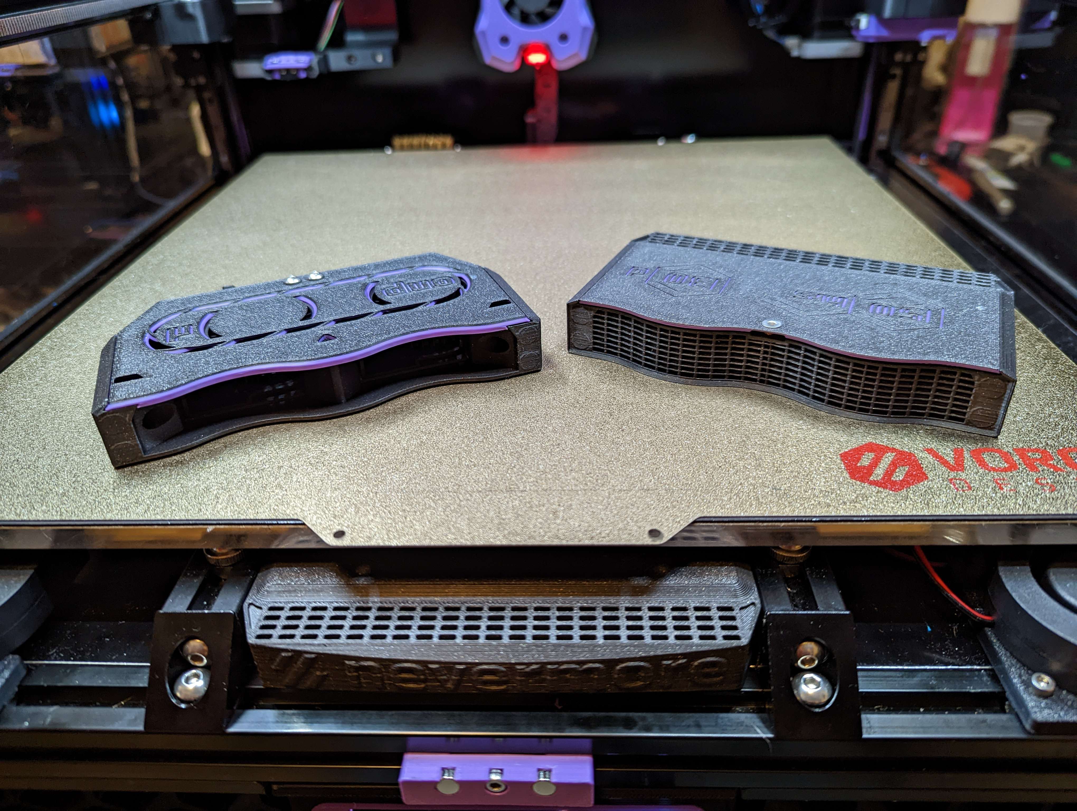
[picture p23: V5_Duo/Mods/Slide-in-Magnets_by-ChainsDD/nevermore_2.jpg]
Mating faces

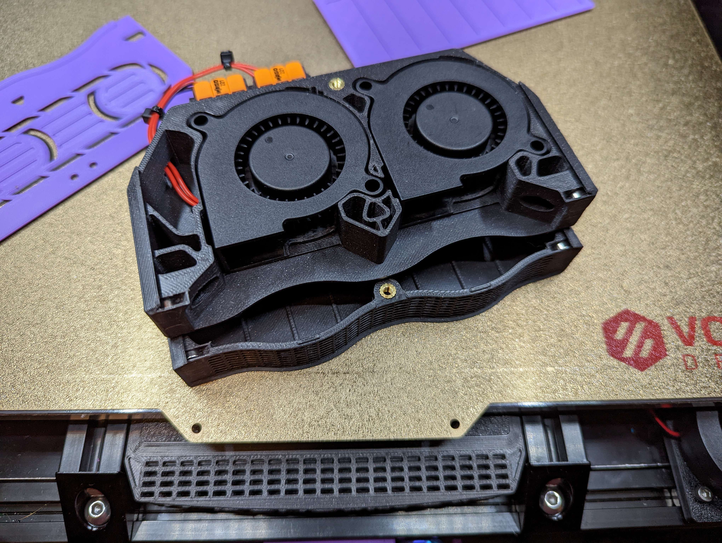
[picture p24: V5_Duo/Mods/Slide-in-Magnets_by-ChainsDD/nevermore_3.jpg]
Magnet slots


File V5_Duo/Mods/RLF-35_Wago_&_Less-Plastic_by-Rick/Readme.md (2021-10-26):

Nevermore Micro **Naked Mod for the PABST RLF-35 Fan mount**.

> Hey! RLF-35 fans are crazy expensive! They are literally $50 per fan.
>
> Buy them used/surplus in EU from www.maranos-shop.de, or world-wide on AliExpress. That way, you can get them for about $12-15. Still expensive, but will hopefully last long enough to become a more economical option than cheap 5015s that needs to be replaced.

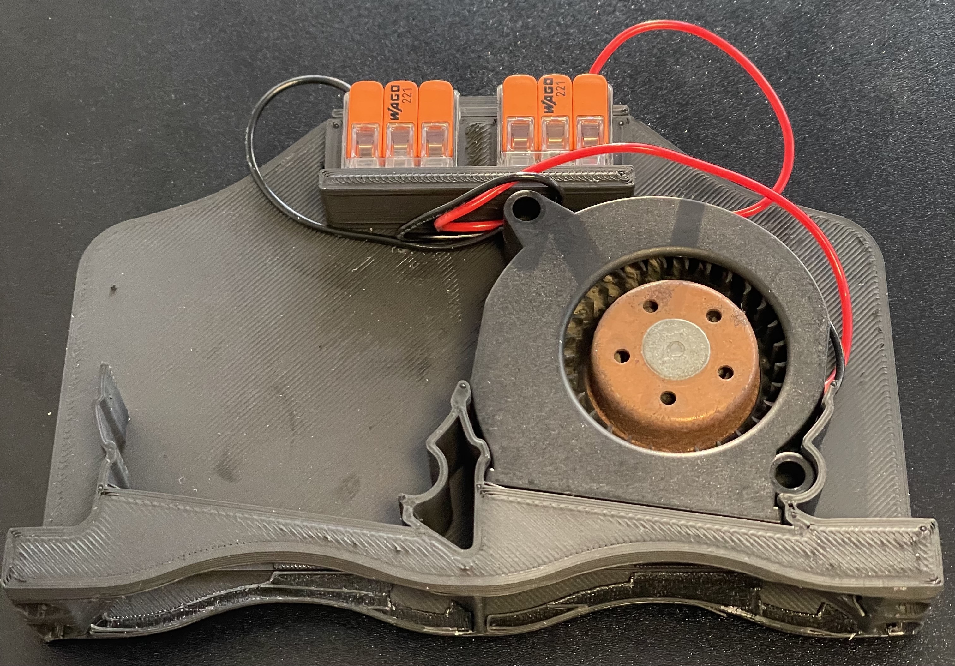
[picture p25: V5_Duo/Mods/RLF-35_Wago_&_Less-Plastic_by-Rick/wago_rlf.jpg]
Less_plastic_RLF_by_Rick Less Plastic! And Wagos!
.

This is a mod of the Pabst RLF-35 fan mount to remove all of the Nevermore Micro exterior casing and keep the mounting as minimalist as possible.
It has mounts for the Wago 221-413 Compact Triple Mount Connector - 2D and 3D models and some details available here:
[https://autodesk-fusion.partcommunity.com/3d-cad-models/sso/221-413-compact-splicing-connectors-for-all-conductor-types-3-conductor-terminal-block-wago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]

The Pabst fans require no modifications and if you are using the Wago 221-413 connectors no soldering is required.

You will need four 3x6 cylindrical magnets to attach the Nevermore Micro Carbon Air Filter Cartridge. If you intend to mount it to 2020 extrusions too will need 2x (M3x12 SHCS) and 2x (M3 2020 T-Nuts).
The Pabst RLF-35 fans are 24v so you will need to find an appropriate power source from your MCU Board or somewhere else. The fans are just a press fit into the mount and the Wago 221-413 connectors slide horizontally into their mounts - they are a tight fit.

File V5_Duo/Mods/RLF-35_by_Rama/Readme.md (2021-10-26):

# Nevermore RLF-35

> Hey! RLF-35 fans are crazy expensive! They are literally $50 per fan.
>
> Buy them used/surplus in EU from www.maranos-shop.de, or world-wide on AliExpress. That way, you can get them for about $12-15. Still expensive, but will hopefully last long enough to become a more economical option than cheap 5015s that needs to be replaced.

## Test 1 (LID)



## Test 4




## Test 3






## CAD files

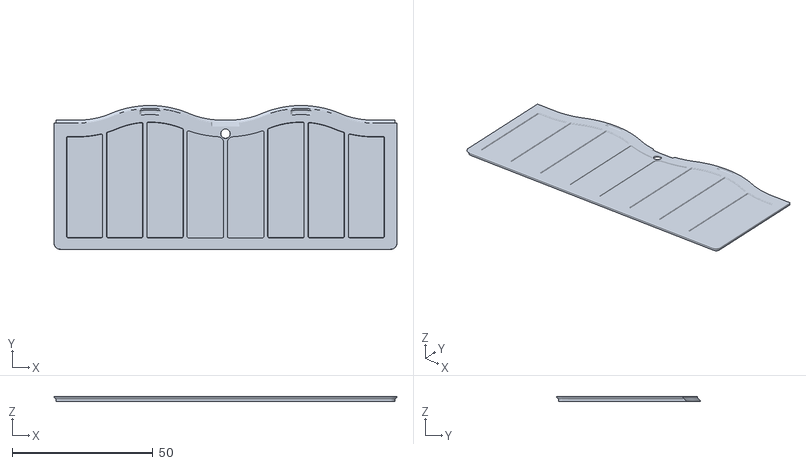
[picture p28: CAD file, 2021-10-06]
V5_Duo/1.8/Duo_Cartridge_LID.stl
122.0 x 51.2 x 1.78

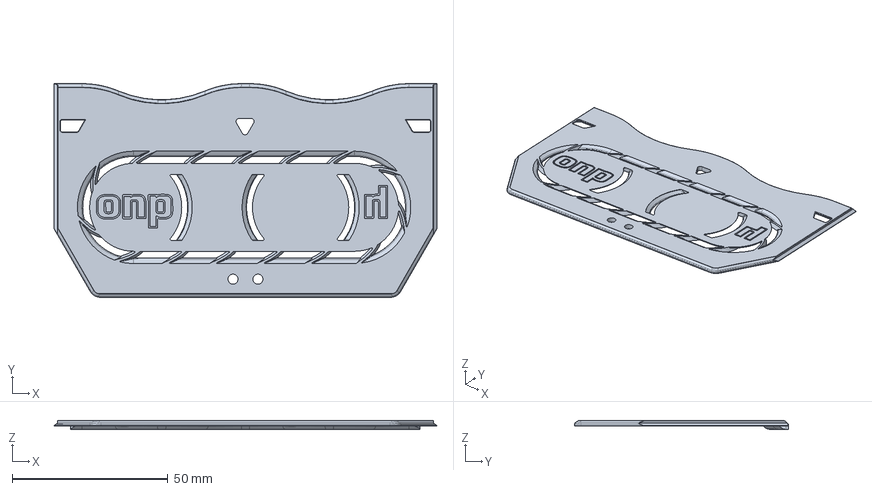
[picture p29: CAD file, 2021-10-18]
V5_Duo/Duo_Plenum_Lid.step
122.8 x 68.5 x 2.80 mm

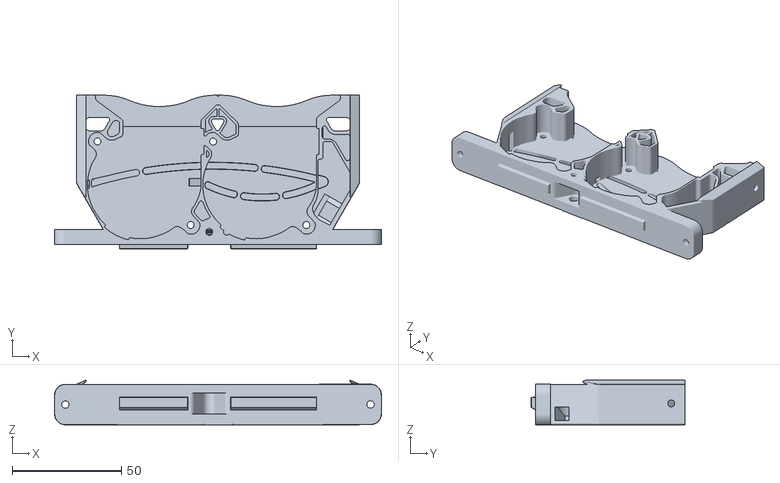
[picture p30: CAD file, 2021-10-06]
V5_Duo/Mods/Rear-Backmount-Plenum_by-mvieleers/mvieleers_nevermore_plenum_backmount.stl
150.0 x 70.5 x 20.5

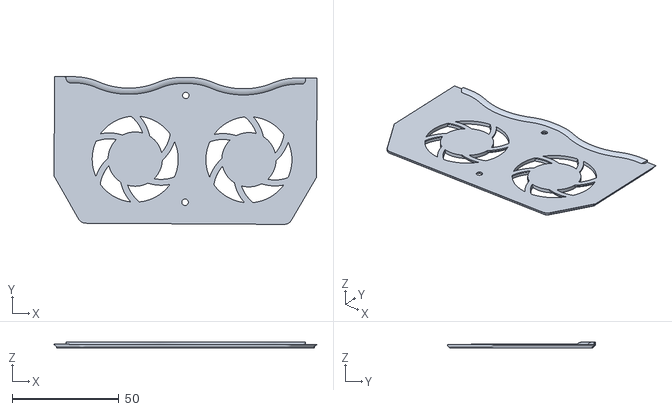
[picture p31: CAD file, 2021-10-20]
V5_Duo/Mods/RLF-35_by_Rama/Nevermore-RLF35_LID_v01_by_Dave.stl
123.1 x 69.2 x 2.81

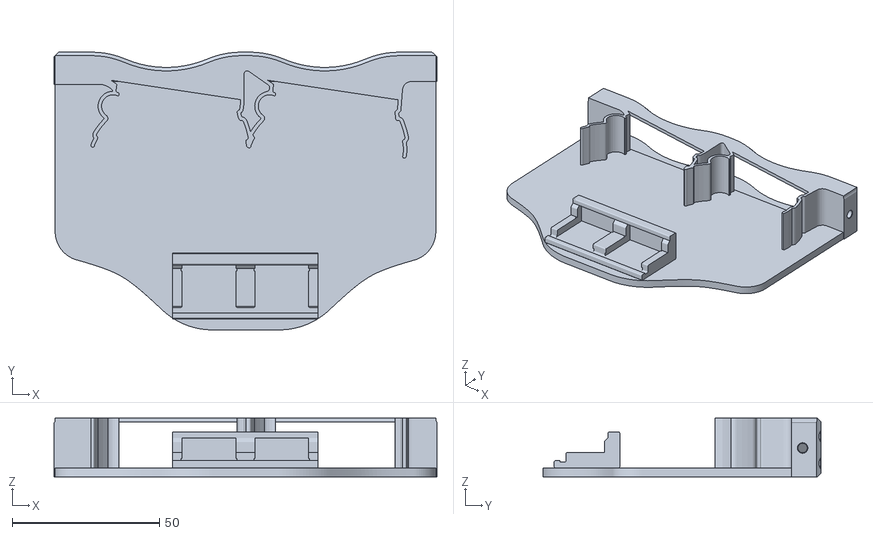
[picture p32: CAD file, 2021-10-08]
V5_Duo/Mods/RLF-35_Wago_&_Less-Plastic_by-Rick/Naked_RLF-35_with_Wago_Triples_Mk1.stl
130.0 x 94.3 x 20.0

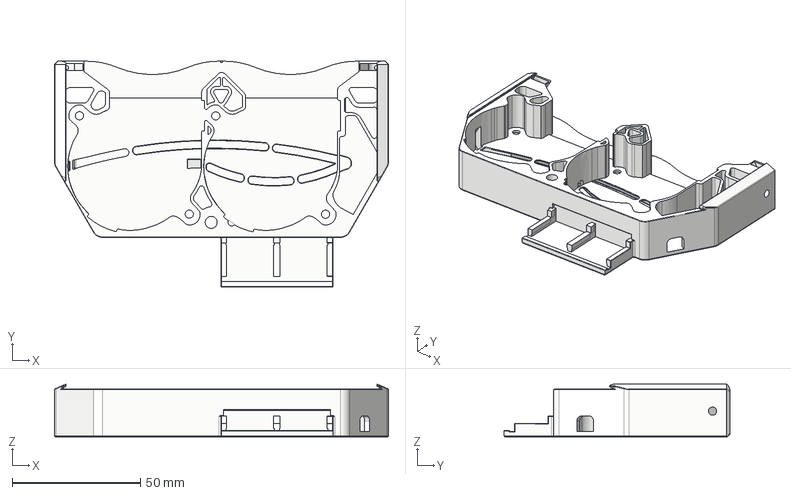
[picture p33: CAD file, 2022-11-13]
V5_Duo/Mods/Slide-in-Magnets_by-ChainsDD/Duo_Plenum_Wago.step
130.0 x 87.8 x 20.5 mm

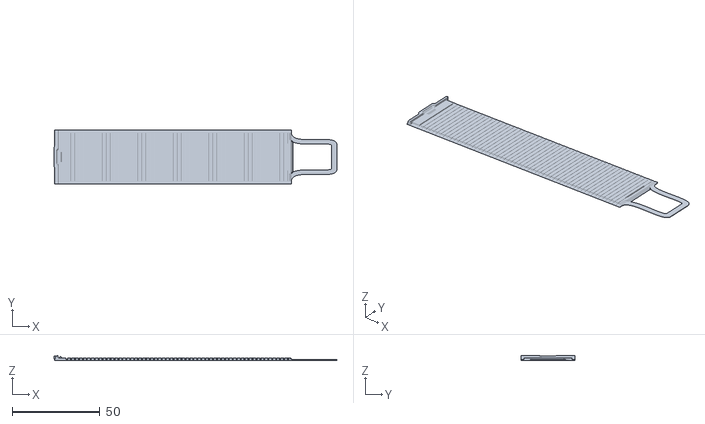
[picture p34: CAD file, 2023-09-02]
V6/STL/[a]V6_Jalousie_Slicer[TAB][THIN].stl
161.4 x 30.8 x 2.66

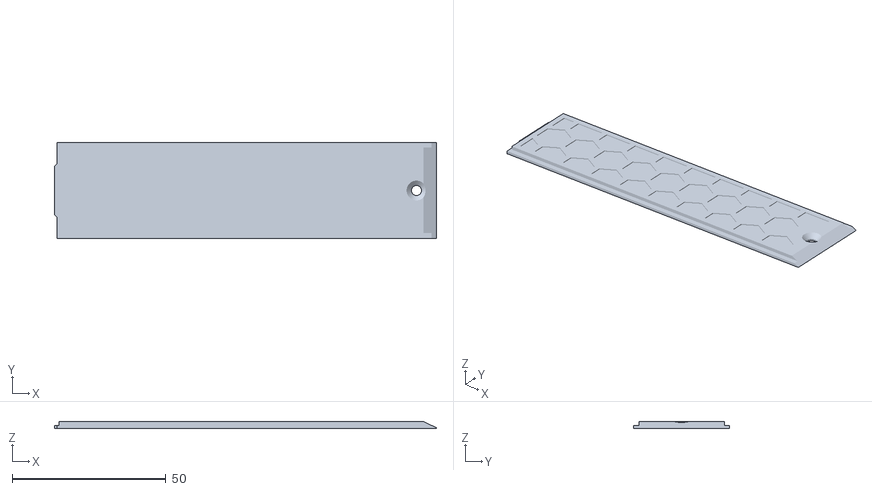
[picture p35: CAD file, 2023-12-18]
V6/STL/Alternate_Cartridge_door_Mod/Sliding_door.stl
124.0 x 31.2 x 2.20

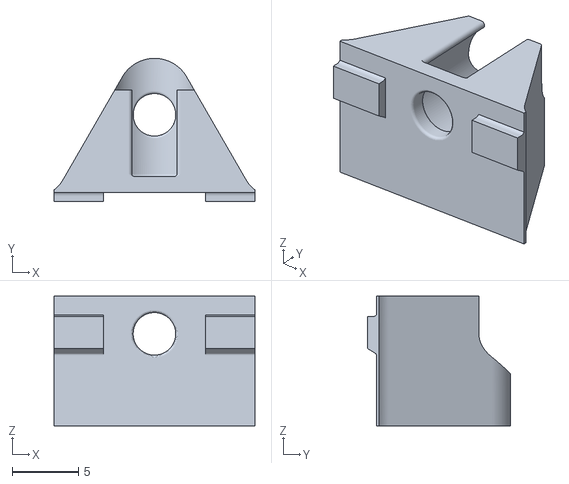
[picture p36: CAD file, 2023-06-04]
V6/STL/Optional_stuff/1515_Frame_Connector.stl
15.1 x 10.8 x 9.79

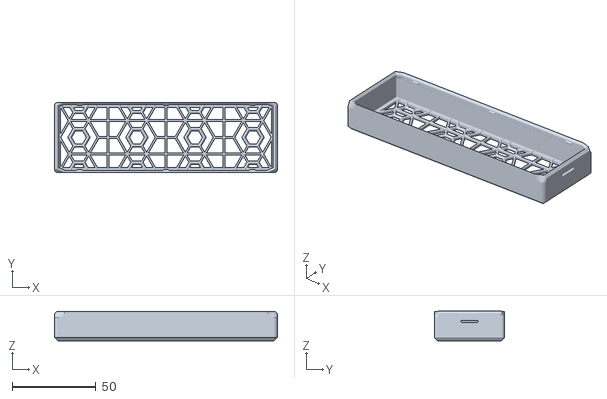
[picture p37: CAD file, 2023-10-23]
V6/STL/XL_HEPA_Cartridge/2_XL_HEPA_Container[reg].stl
133.2 x 42.0 x 17.7

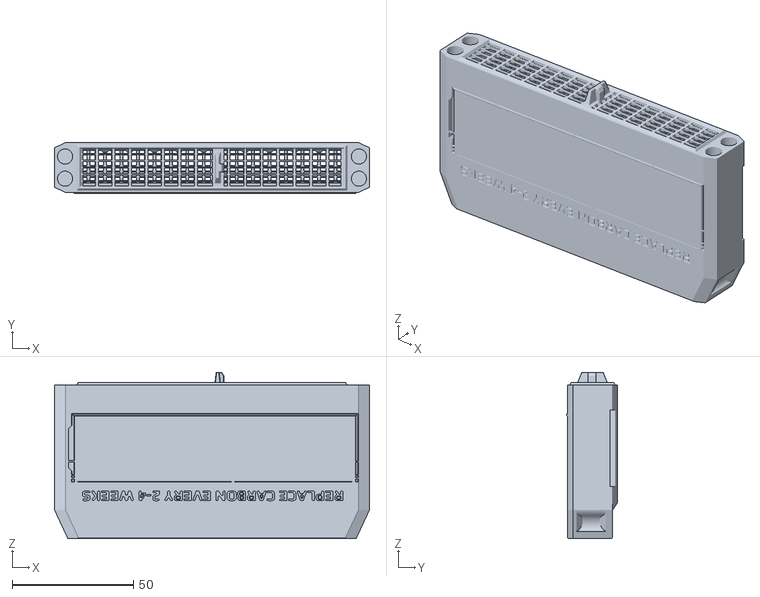
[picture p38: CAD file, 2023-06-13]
V6/v0/v0_Straight_Cartridge.stl
130.0 x 21.0 x 68.7

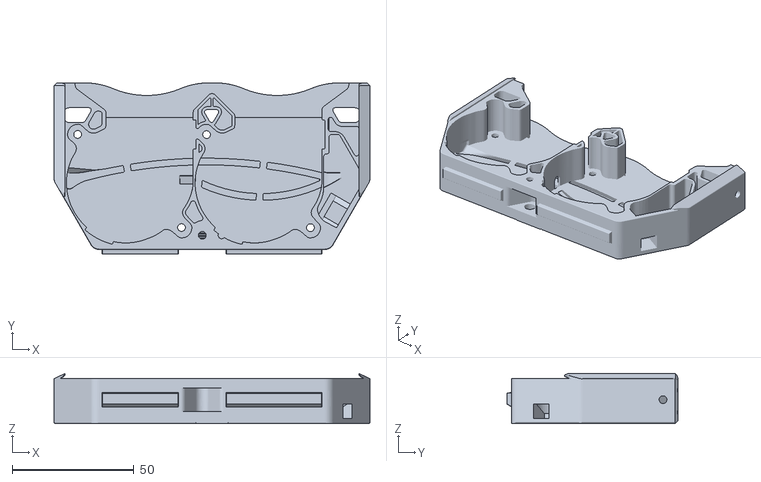
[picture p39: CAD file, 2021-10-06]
V5_Duo/1.8/V1_Duo_Plenum.stl
130.0 x 70.5 x 20.6

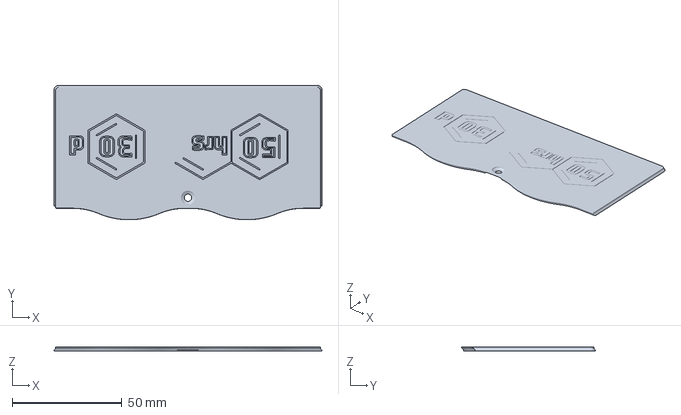
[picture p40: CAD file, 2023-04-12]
V5_Duo/V2/XL_Cartridge_Lid(contributed_by_Bucknova).3mf
122.0 x 61.2 x 1.78 mm

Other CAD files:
V5_Duo/V2/Regular_Cartridge_Lid(contributed_by_Bucknova).3mf
V5_Duo/Duo_Plenum_RC7_DELTA.stl
V5_Duo/Mods/RLF-35_by_Rama/Testing_Nevermore-RLF35_LID.stp
V5_Duo/Mods/RLF-35_Wago_&_Less-Plastic_by-Rick/Nevermore_RLF35-v4_Naked_with_triple_Wagos_v5.step
V5_Duo/Mods/Slide-in-Magnets_by-ChainsDD/Duo_Plenum_backmount.step
V4/BASES_V1.stl
V4/BASE_V0_1515.stl
V4/BASE_V2.stl
V4/Nevermore_Micro v4.f3d
V4/V4_4x6_magnets/FAN_PLENUM_4_6.stl.stl
V4/V4_4x6_magnets/FAN_PLENUM_LID_4_6.stl
V4/V4_4x6_magnets/FAN_PLENUM_LID_4_6_by_Dom186.stl
V4/V4_4x6_magnets/FILTER_CARTRIDGE_4_6.stl
V4/V4_4x6_magnets/FILTER_CARTRIDGE_6_3_DirectedUp.stl
V4/V4_4x6_magnets/FILTER_CARTRIDGE_LID_4_6.stl
V4/V4_4x6_magnets/FILTER_CARTRIDGE_LID_6_3_DirectedUp.stl
V4/V4_4x6_magnets/base_fix.stl
V4/V4_6x3_magnets/FAN_PLENUM_6_3.stl
V4/V4_6x3_magnets/FAN_PLENUM_LID_6_3.stl
V4/V4_6x3_magnets/FAN_PLENUM_LID_6_3_by_Dom186.stl
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

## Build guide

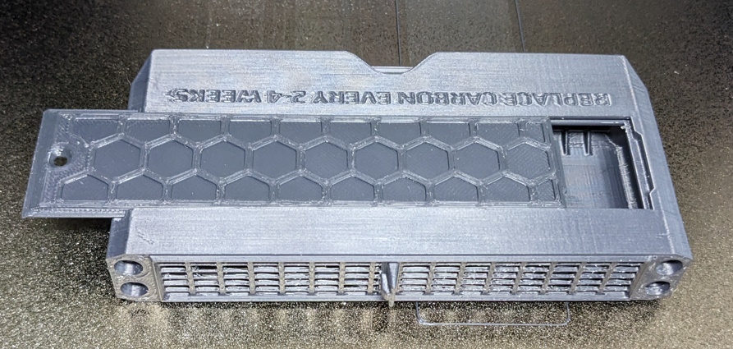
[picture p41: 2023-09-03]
V6/STL/Alternate_Cartridge_door_Mod/After_Printing.jpg

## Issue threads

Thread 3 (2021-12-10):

V5 Cartridge Lid CAD files

westminsterflip, 2021-12-10:
I did not see a cartridge lid in any of the cad files so I was hoping to get the f3d/step file for that if possible

eduncan911, 2021-12-11:
I can confirm, it's missing the STEP for the Cartridge Lid.  I think we should clean up that root folder as most should be using V0/V1/V2/Mods folders.

If you are looking for the STLs to print, you can find two different sizes here: https://github.com/nevermore3d/Nevermore_Micro/tree/master/V5_Duo/V2

Sadly, I cannot install F360.  So I am unable to view the f3d files.

ping @0ndsk4

0ndsk4, 2021-12-11:
Added it to the root directory. Thanks.

Closed 2021-12-11.

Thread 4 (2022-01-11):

Question : Granules vs Pellets?

PhilBaz, 2022-01-11:
Would the micro v4 or v5 work with granules rather than pellets? I could sift of any dust. Do you see a problem with that plan?

eduncan911, 2022-01-12:
I'll let @0ndsk4 chime in.

Until then, IMO the irregular surface area of granules would mean you could have some blockage from two or more pieces clumping together.  Whereas pellets generally wouldn't clump no matter how they are shifted around.

0ndsk4, 2022-01-12:
TLDR - Granules are good too.
Pro: Often slighter higher efficiency/surface area due to intact porosity/structure compared to pellets that are extruded with a binding agent.

Con: more dusty, generally much higher pressure drop. 4x6 mesh are big enough particles to have equal pressure drop compared to 4mm pellets. 4x8 is comparable to 3mm pellets, and generally have a lot poorer air flow with 5015 fans - if using these make sure you have a high static pressure fan and don’t pack it (sprinkle fill the cartridge).  Anything smaller than 4x8 is unusable.

PhilBaz, 2022-01-12:
Thanks for the info, very helpful. I would buy nevermore carbon, but alas I live in the frozen northern tundra known as Canada, and shipping ain't cheap!

Two quick questions...

1) roughly how many grams of carbon fill the V4 or V5
2) In the V5 folder, which files am I supposed to use? V5/V2?

0ndsk4, 2022-01-13:
Good carbon is lighter (more porous) so weight is a bad metric. But about 50 grams.

Naming scheme is for voron machines (ie Voron 2.4, V2, or Voron 1.8, or V0). For general use and placement on a 2020 extrusions machine, V1.8 is most versatile.

For Canada, the guy running Jurassic Carbon (Toronto) has been vouched for on discord. His 4mm Anthracite pellets is a very good option for printer fumes.

PhilBaz, 2022-01-13:
Thank you!!!

I found a local supplier with 4mm CKV4 carbon pellets....

Just need to look into the CKV4 designation a bit more closely... Im hoping these will work out.

Closed 2022-01-12.

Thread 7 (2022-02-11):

Nevermore Micro v4 - lid and cartridge collision

narodo, 2022-02-11:
Hi guys,

First of all thanks for this awesome project!

I printed the parts (directly extracted from the Fusion 360 project) for the Micro v4 but have some problems when assembling.
The lid does not cover the cartridge fully. There is a gap on one side.
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

I had a look at the Fusion360 model and it seems this actually to be expected (I only assigned a different colour to make it easier to spot, otherwise this is a fresh unmodified download).
You can see that there is a collision and that the two curves don't match up:
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

If I rotate the lid by about 0.5° until the two curves are fairly well aligned, I can reproduce the gap I see in my real-world print:
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

Is that a known issue?

Thanks!

narodo, 2022-02-11:
Ok, nevermind... I made a stupid mistake. I printed the lid and cartridge lid as one piece.
When those parts are separate pieces I assume the small misalignment will not have any real consequence.

Closed 2022-07-09.

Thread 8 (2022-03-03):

how to protect carbon if not printing around the clock?

bubnikv, 2022-03-03:
Hello.

Reading the instructions at your distributor
https://lecktor.com/en/v2x-misc/870-nevermore-carbon.html
and other sources I got that carbon will be depleted if exposed to the air.

Now if I do not print regularly and I want to use the product referenced above for more than 6 months, what is the recommended procedure?

What is the shelf life of the vacuumed carbon?

What is the shelf life of the bag if the vacuumed bag was opened and then sealed just with the bag seal?

Would you please consider selling smaller vacuumed packages so that if one does not print ABS regularly, one can keep the carbon fresh longer?

Does it make sense to remove the whole filter assembly filled with fresh carbon from the printer and seal it into a sealed bag between prints to keep the carbon fresh? This is something I would consider as a good nature friendly practice.

Thanks for a great product.

0ndsk4, 2022-04-25:
Hi, sorry for being inattentive!

* Shelf life is about 2 years for activated carbon, even when stored air tight (it will work after that too, just not as great).
* If stored in an air tight container (ie a good bag seal), shelf life is almost the same. The carbon will only be exposed to VOCs whenever you break the seal, a for a few short seconds/minutes.
* If there’s demand for it, sure. But the bag is pretty small already, and two years to use it so… also, with the exception of possibly natural PLA and PETG in a well ventilated space, it’s a good idea to use the carbon for other filaments as well.

* removing the cartridge and putting it in a sealed plastic bag between prints would increase filtration duration, possibly by quite a lot. But personally, I’d just forget. Lucky we’re all different :)

Closed 2022-04-25.

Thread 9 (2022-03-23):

BOM error - Magnets are '3x6' not '6x3'

RudyAlbertoAcostaMarmalade, 2022-03-23:
As the title states - I now have to find some creative use for some very long and thin cylindrical magnets :D

Thank you for taking the time to develop the Nevermore!

wkeifenheim, 2022-04-18:
I nearly made the same mistake, but when I couldn't find 3x6 magnets on Amazon I read closer and saw in the v5 changes section states `BOM 3x6 magnets are standard`. Standard BOM is 6x3 so I then compared the v5 plenum to other Voron V2 parts and confirmed that the BOM listing should state 6x3.
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

wkeifenheim, 2022-04-18:
Someone has already submitted a PR to fix this: https://github.com/nevermore3d/Nevermore_Micro/pull/5

0ndsk4, 2022-04-25:
Thanks, is corrected in the V5 BOM section now!

Closed 2022-04-25.

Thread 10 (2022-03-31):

Suggestion: Implement support for 3M bayonet-style filters, e.g. 6003 OV/AG, or similar

VIXIVIXIV, 2022-03-31:
Performance-wise, this should be the best option; these filters are NIOSH approved (granted, only for use with a compatible facepiece) for keeping organic vapor exposure under exposure limits (while the paper documentation is not too clear on what "organic vapors" encompasses, 3M's service life calculator ([https://sls.3m.com/](https://sls.3m.com/)) provides a wide range of potential contaminants to check filter compatibility and lifespan against).

Arguments can be had about the economy of the filters, but the calculator suggests reasonable lifespan before reaching its built-in exposure limits, which are very conservative (e.g. the calculator will report time to reach breakthrough of 10% of the exposure concentration or half of the OSHA exposure limit, whichever is lower, at which point the cartridge will likely still outperform brand-new loose carbon). The cost of a pair of cartridges is about $14, if bought in bulk that drops to about $10 a pair, and a single cartridge is likely sufficient for this application (the respirators use 2 cartridges in parallel to reduce the restriction on breathing and improve comfort, for the Nevermore the added restriction of a single cartridge can be overcome with more powerful fans). The cartridges would also be easier and faster to replace and have a wide range of options available for different VOC contaminant profiles or particle filtration performance.

If that still proves too expensive, users also have the option of purchasing knockoff/off-brand cartridges, such as [these](https://www.amazon.com/Trudsafe-Organic-Replacement-Cartridge-Respirator/dp/B07Z7MFG22l).

0ndsk4, 2022-04-25:
There are several 3D printer adaptions for 3M breather cartridges out there. While cost is one part, a respirator if made for high pressure (breath is 50-100x stronger than a fan)  / low volume (breath is 0.22cfm).

If we run 2cfm through a filter made for 0.22cfm it would likely deplete 10x faster too. All in all, I’m
 It sold on the idea.

Closed 2022-04-25.

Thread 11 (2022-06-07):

Artefacts in Nevermore Area

DietZnX, 2022-06-07:
Hello , I print the V2 Duo_Catridge and found some artefacts in the front area on my print . I see that it comes from the stl . Enclosed some pictures . !

I love the Nevermore ! Thank you for that :)

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

0ndsk4, 2022-07-09:
Strange, I'll investigate that. Thanks.

MandicReally, 2022-09-11:
Came to point out this same thing. Had hoped to just re-export the STL as it looks like a bad export to me, but the CAD files don't seem to include either cartridge housing.

bucknova, 2023-03-29:
Verified artifacts on STL file.
Will look into clearing up.

bucknova, 2023-04-01:
Inspected F3D files. Artifacts are not on original models.
I will export and re-upload the STL files.

bucknova, 2023-04-10:
Cause of artifacts determined to be extruded text and fillets.

Reworked the texts, and filleted to a smaller degree. New design has a cleaner topography and tessellates better in slicing software.

I will update all remaining pieces. After the parts have been updated for support material, they will be published.

Neolker, 2023-04-12:
Can I just ask for this part, I've been waiting for it for quite a while, or will there be major changes on the other parts as well so I have to wait anyway? Thanks in advance.

bucknova, 2023-04-12:
Files have been updated.
I will have them pushed to the GitHub shortly.

Issue has been resolved.

Closed 2023-04-12.

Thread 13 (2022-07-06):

DUO XL 3mf slices without bottom

00Roc, 2022-07-06:
Cura slicer will slice/print the latest Duo XL 3mf without a bottom.

SuperSlicer acknowledges different parts of the file and asks if they are part of the same object and resolves whatever issue Cura cannot.

So - the 3mf file cannot be sliced w/ CURA, but can function w/ SuperSlicer.

0ndsk4, 2022-07-09:
Ok, I'll try to upload it as a stl as the positioning data of the 3mf causes some issues.

It will slice fine with cura, but you first have to select both bodies, right click and group them, then drag them above the build plate.

Closed 2022-07-09.

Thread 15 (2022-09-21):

Update DUO_plenum.f3d with front edge chamfer

ChainsDD, 2022-09-21:
The CAD file is missing the chamfer around the edge of the mating surface. This makes it difficult to make a modded plenum that mates with the cartridge properly.

bucknova, 2023-04-12:
Verified missing chamfer on v2 of the DUO_Plenum file.
Added chamfer to plenum and lid.
Update will be published.

Issue resolved.

Closed 2023-04-12.

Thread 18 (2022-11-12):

VOC Monitoring Question

MammothTanker114211, 2022-11-12:
Hello, I am looking to gain more information on VOC monitoring. The Nevermore Max readme contains info on VOC monitoring, and references research from Dr. Dave. Does the nevermore team have a link to his research, or know of any VOC sensors that are well suited for FDM printing. Thank you
 "Ever wondered when  its time to swap carbon? Well, on the max you could add VOC sensors to both intake
and exhaust and measure how well the filter is doing its job! Thanks to **Dr Dave**
there are even data on which sensors reliably detect the aromatic VOCs we strive
to catch (a lot of sensors hardly detect extrusion VOCs at all as they are intended
for other applications)"

0ndsk4, 2022-11-13:
Currently, VOC sensors are quite inferior to our own noses.

As of now, we know SPG30/40 VOC sensors does reliably detect ABS extrusion, BME680/688 does not, and ENS160 is somewhere inbetween. But the step from detecting extrusion to having a useful implementation is huge, there are simply a huge amount of variables (the largest being how much residue is on your panels already when installing a filter...). And even when simply using the delta of intake/exhaust, voc figures change with air speed, and during long prints (24h+) sensor readings regress towards the mean no matter the pollution. There's a  lot needed software side for a reliable solution, so we're quite far away as of right now.

Closed 2022-11-13.

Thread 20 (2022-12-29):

Will Noctua fans fit?

cdmichaelb, 2022-12-29:
Noctua comes in 5v and 24v variants and tend to be very quiet.

0ndsk4, 2022-12-29:
Carbon filters have high pressure drop when thick enough to catch VOCs. That means high static pressure, which means blower type fans or server fans.
Noctua fans are axial with very low static pressure. They will not push enough air through thick filters (for reference, axial noctuas are between 0.5-4 mmH2O or pressure compared to blowers that has 15-25 mmH2O.

afaik, noctua has neither high-rpm server fans or blowers, and wouldn’t be very suitable. Open for suggestions though!

Closed 2022-12-29.

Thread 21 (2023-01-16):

Clarify whether supports should be enable during printing

countspongebob, 2023-01-16:
Can figure this out by trial and error, but a quick note in the writeup would be awesome help for someone coming to the project for the first time.

0ndsk4, 2023-01-22:
Thanks. Added a line under assembly. will try to clarify further in the future.

Closed 2023-01-22.

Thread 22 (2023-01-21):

Revise V5 BOM Heatset insert locations for plenum

Flipsoul, 2023-01-21:
1x Plenum base to Plenum lid joint
4x for Fan tabs (2 ea fan)
---
Total 5x at Plenum

Also, it seems most assemblies people are making omit the heatset inserts and SHCS that go into the fan tabs, while adding the fastener in cartridge base to lid joint. including referenced assembly pictures for V5.

MarcelRobitaille, 2023-05-07:
Also curious about this. It seems like the numbers don't add up in the readme.

Shouldn't it be 6 total?
- 1x in plenum base to secure plenum lid
- 1x in cartridge base to accept cartridge lid
- 4x for fans

I'd be happy to take pictures for the gallery and make a PR updating the readme if I could get some confirmation that this is correct.

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

0ndsk4, 2023-05-08:
Hi, true, bom is for the original mounting position in a voron v2, where the base insert isn’t used. A clarification that a fifth (sixth in total) insert is needed for panel mounting on a 2020 extrusion is a good idea. Please proceed :)

0ndsk4, 2023-05-08:
Blind hole shouldn’t be there. Originally I just put it there for symmetry and had a short blind bolt in it. I’ve since gotten used to the fact the useful hole is off center.

Closed 2023-05-08.

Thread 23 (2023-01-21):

V5 Slide-in Magnet mod interference with lip on lid

Flipsoul, 2023-01-21:
Slide in magnet mod adds slots for magnets to roll-in on at front of plenum. These interfere ~1.5 mm with the lip on the plenum lid. easy to clip the added feature back. But it seems it could be reduced without loss to printability or function

mechatroniks-git, 2023-01-24:
I'm looking at the CAD model, getting ready to print this. I'm not seeing any interference. Can you confirm where you are seeing it?

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

Flipsoul, 2023-01-25:
i wont be able to verify or get pictures till the end of the week, but i believe my particular issue was between prints of
Nevermore_Micro/V5_Duo/Mods/Slide-in-Magnets_by-ChainsDDNevermore_Micro/V5_Duo/Mods/Slide-in-Magnets_by-ChainsDD/Duo_Plenum_wago.stl
And
Nevermore_Micro/V5_Duo/V2/V2_Duo_Plenum_LID.stl

There are a quite a few different solid model files/mesh files, so its possible i have a mismatch

Flipsoul, 2023-01-25:
Looks like it was a mismatch. I'm seeing more files within the slide in magnet mod folder than i did before including the plenum lid file, which i want seeing before. (Couldn't see any of the images in the plenum lid file before too) Not sure why i want seeing them before.

Closed 2023-01-25.

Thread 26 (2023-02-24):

Provide the f3d for the 6x3 magnet verion

jjfs127, 2023-02-24:
I love the design but I wanted to modify the [FILTER_CARTRIDGE_6_3.stl](https://github.com/nevermore3d/Nevermore_Micro/blob/master/V4/V4_6x3_magnets/FILTER_CARTRIDGE_6_3.stl) to add some text around the side. Made some modifications with the [Nevermore_Micro v4.f3d](https://github.com/nevermore3d/Nevermore_Micro/blob/master/V4/Nevermore_Micro%20v4.f3d) file once imported into F360 only to realize after I printed it that the holes for the magnets were quite small. I would appreciate a way to use the f3d with the regular 6x3 magnets or at least have the holes parameterized in Fusion. Thank you.

Closed 2023-03-09.

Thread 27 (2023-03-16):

Improvements to the readme for new users

LiSongMWO, 2023-03-16:
I'm a new user and I read the `readme.md` and while it left me more informed on VOCs and carbon in general, it didn't actually help me better understand the build, and how to integrate it into a printer, or what it actually is (i.e. will I be able to use it?). I had to find some random dude on youtube doing a video on installing it (and installing it in a bad (hot) location) before I understood what and how. The shiny renders look nice but they don't really give me much information, I'd much rather have seen an exploded diagram of the main parts and how they connect/attach to a printer.

The biggest thing I missed was an overview of how it's meant to be used and installed. Something like the following at the top of the readme would have helped me greatly: "Nevermore Micro is a recirculating activated carbon air filter installed inside of a sealed print chamber. Typically it's installed by attaching to the printer's t-slot extresions or VHB taped to the chamber walls. It needs one free 12V/24V fan header on your control board and firmware support (e.g. klipper)."

Additionally while there's a lot of good information on the readme, it's very long and a bit unfocused. My suggestion is to move historical context and background on VOCs etc to a separate (github wiki?) page and focus the readme on building, BOM, sourcing and installing linking out to the above pages in the introduction.

And thanks for this cool upgrade :)

agravelot, 2023-06-08:
Here is a documentation which can be useful: https://www.ldomotion.com/p/guide/18295873486193941

jwyse, 2024-02-01:
LDO moved their guides:
[Nevermore V5 Duo - V2.4](https://www.ldomotion.com/p/guide/Nevermore-V5-Duo)
[Nevermore V5 Duo - Trident](https://www.ldomotion.com/p/guide/Nevermore-V5-Duo--Trident)

FJRPilot, 2024-02-11:
I would also chime in and suggest that specific instructions be added regarding recommended print orientations for the V6 Micro.  Importing the STL's bring the Plenum and Cartridge into slicers vertically. If you attempt to slice you will get errors about "Floating Cantilever's" and asked to re-orient the objectsS
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

jwyse, 2024-02-12:
> I would also chime in and suggest that specific instructions be added regarding recommended print orientations for the V6 Micro. Importing the STL's bring the Plenum and Cartridge into slicers vertically. If you attempt to slice you will get errors about "Floating Cantilever's" and asked to re-orient the objects

The default orientation (vertical) is actually the recommended orientation.  Orca's floating-cantilever warning can be ignored.  A note in the readme to clarify this would be nice.

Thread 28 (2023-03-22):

Size of the magnets to slide

59marcopolo, 2023-03-22:
Hello,
What is the size of the magnets to slide?
The 6x3mm don't fit.

bucknova, 2023-04-12:
Inspecting the file, the magnet holes are 6.25mm in diameter with a depth of 3.2mm.
The extra space for the magnet allows for variations in printed tolerances from your printer.

Issue can be closed.

Closed 2023-04-12.

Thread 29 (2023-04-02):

nevermore V5_duo - Plenum lid make fans loud and weak!

Hrumque, 2023-04-02:
The project looks very nice optically, but in practice - I had my doubts when printing, and the first launch confirmed them.
Very nice cover over the fans - it has a very narrow airflow channel. It chokes the fans. After putting it on, you can immediately hear the fans go to high speed - it means that they spin the air in a circle, instead of pumping it through the filter.

The first mod - I cut out the entire inner part of the lid with a weight. The fans are exposed.
I measured the air flow - almost 50% better flow with such a cut cover. And almost 6dB quieter operation (at full 24v power supply)

Because my pliers-cut cover looked ugly - I printed a new one, as in the picture - already with holes cut out for the fans.
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
Success.
Quiet (well, maybe not super quiet, but quieter than the original) with higher airflow. As a result - you can set almost half the power supply - there is the same air flow and it is very quiet.

thenickdude, 2023-04-02:
6dB is huge, could you share your STL? I'd love to try it too.

thenickdude, 2023-04-03:
Makes sense, I'll try that too

0ndsk4, 2023-04-10:
Thanks for this. Changing the lid design shortly.

bistory, 2023-05-21:
> 6dB is huge, could you share your STL? I'd love to try it too.

If you want, here is a quickly modded lid (I just cut 38mm holes into the existing lid)
[LID.stl.zip](https://github.com/nevermore3d/Nevermore_Micro/files/11524019/LID.stl.zip)

I'm printing it right now :-)

0ndsk4, 2023-06-02:
Thanks. Testing has shown the lid design wasn't optimal. This "bug" has now been squashed in the new Micro V6. When cad files are online its likely possible to use them to update the V5 lid for people who do not wish to upgrade their micros.

Closed 2023-06-02.

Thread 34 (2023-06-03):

STL files are missing?

kkingengineering, 2023-06-03:
Heads up - there are no STL/STEP files in the git for Micro V6. Did they not upload? Would like to start printing this asap. Thank you for your work.

0ndsk4, 2023-06-03:
Just making sure things will print as good for others too before uploading or instructing anything officially. Today I learned it good if the jalousie lid is heated upon first insertion, and made a few edits to lessen the chances of failure. You’re welcome to test the beta release files on Nevermore discord in the meantime: https://discord.gg/pgppCmjA

Closed 2023-06-03.

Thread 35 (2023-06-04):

[V6] Unsupported overhang issue on plenum

max-cz, 2023-06-04:
Hi

Is this an errors or how is the printer going to print these?
Layer 347.
Sliced with PIF standard in Orca and Superslicer.

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

scheini79, 2023-06-04:
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

You need to turn it 90 degree. You’re printing it in the wrong direction.

eambos, 2023-06-04:
This issue was reported on the Nevermore Discord. It's due to a 0.4 degree misalignment.
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

scheini79, 2023-06-04:
> This issue was reported on the Nevermore Discord. It's due to a 0.4 degree misalignment.
> 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

But in his picture it’s clearly standing, not laying flat.

0ndsk4, 2023-06-04:
Thank you. As noted, somehow the bridge had a 0.4 degree angle causing it to be sliced in half. It’s been corrected in the cad file, and a new stl export will be up soon!

Closed 2023-06-04.

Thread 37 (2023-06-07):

Built in supports fail

kkingengineering, 2023-06-07:
Printed in ASA using same settings as all other Voron parts I have made. These settings usually make clean results. Maybe an adjustment on this support so it anchors better on the left side? Maybe post a version with no built in supports so we can attempt via our own slicer? Thx.

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

0ndsk4, 2023-06-08:
Thanks. I’ve seen supports fail on both sides for some users. I’ll look into it and if all else fail export a file without the supports.

Closed 2023-06-08.

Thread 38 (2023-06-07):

V6 STL files have unprintable fragments

Vykori, 2023-06-07:
The STL files for the Jalousie, and to a lesser extent also the Plenum and Cartridge, are detected as having lots of objects in 1 file. For instance in Super Slicer, the "Split to Objects" or "Split to Parts" functions will reveal all of the tiny pieces that are too small to print

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

0ndsk4, 2023-06-08:
Are there any images, the jalousie has a lot of small gaps everywhere to force the slicer to print the walls in a certain direction in every layer, so I would expect some slicers to object.

Closed 2023-07-20.

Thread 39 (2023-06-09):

V6 Issues

forReason, 2023-06-09:
I am having trouble printing the catridge and the part holding the fans:
For the catridge:
- The support panel is unprintaple, I resliced it, printed at 30mm/s and the support panel just becomes a bunch of spaghetties.

- The part holding the fans has three primary issues for me:
    - The fans provided by ldo do not fit perfectly
    - there are no channeld for the cables
    - the top lit does not fit (its loo long)

0ndsk4, 2023-06-09:
Check out the plenum for sunon geometry fans uploaded today. The regular does fit delta, gdstime and winsinn. The new sunon should work for honeybadger, likely ldo uses sunon geometry as it was recommended for v5.

I have not had a single support failure myself, and am interested in what doesn’t work
1) did you try yesterdays cartridge panel with even more attachment points?
2) do you use a nozzle >0.4mm, making single wall 0.4mm extrusions unreliable? If so what size?
3) do you use 0.2layers and 0.2 bottom layers so the integrated support lines up with layer heights? If not, how it prints can be somewhat slicer dependent. This has been prototyped using cura.

No wire path is a feature, not a flaw:)

johnbarratt, 2023-06-11:
> the top lit does not fit (its loo long)
Seeing this as well as per pic, also is too wide by a few mm:
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

This is with the latest files for v6. Also, FWIW, my supports didn't fail.

Closed 2023-06-16.

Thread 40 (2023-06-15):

Wago 221-2

Zay1Million, 2023-06-15:
The internal wago option isn't an option as it shorts the power and ground wires together, could damage a mainboard. Asking for more information in depth on how you were able to get this to work based on the instructions.

Closed 2023-06-15.

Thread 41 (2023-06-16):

Plenum side mounting holes reversed for a v2.4.

uosdwishpoom, 2023-06-16:
Mounting holes on the plenum sides do not line up in the middle of the 2020 rails on the bottom of a v2.4.  They are offset 2 to 3 mm causing misalignment with the 90 degree filtration medium box.  The filtration box fits snug but fine to the bottom panel on a v2.4 with whoppingpochard kinematic mounts which doesn't leave room to tilt the filtration medium box to the offset plenum.

0ndsk4, 2023-06-16:
Thank you. Don’t know what has happened. Fixing it now.

uosdwishpoom, 2023-06-18:
Thanks for the great work that you do for our health and well being.  Your
designs are outstanding. Looking forward to making a stealthmax when it is
released.

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

Closed 2023-06-16.

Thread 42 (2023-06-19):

v6 - please provide assembly photos

garyd9, 2023-06-19:
A couple of photo's showing the assembly of the v6 would go a long way to making it easier to follow the directions.  While I was able to print and (finally) assemble it, there were a couple of "huh?" moments.

One issue I never managed to resolve to my satisfaction was where to run the fan wires inside the plenum.  Right now, the plenum cover bulges out a bit due not having anyplace to run wires (or not knowing where they should be run.)

Finally, I'm not thrilled with the plenum's "snap close" lid.  If I ever need to open that back up to service a fan or something, I'm not sure I'd be able to do so without breaking the plastic.  If it's secured with a screw, why ALSO make it snap closed?

0ndsk4, 2023-06-19:
Thanks for the feedback, it’s greatly appreciated!

The wire space is the inside hollowed out surface of the lid - there should be close to 2mm for wires with no bulging as long as the wires 1) don’t overlap, and 2) the outermost fan has the wires removed from the fan casing wire path and folded in the other direction so it doesn’t interfere with the thicker edge/rim of the lid. If you want, you can hold the wires with a piece of tape while securing the lid, but once the lid is on it will hold the wires securely with no tedious wire path routing.

As for the lid fastening, Im happy for hear input on getting this to work better. .
Lid is tight and the main “snaps” are located precisely above the fan exhausts to keep an air leak path from forming. The bolt is not really needed, as stated, but was added for high heat applications where plastic wants to deform (v5 lids deformed without a bolt). For the same reason, a single bolt in the center would not keep the edges from warping if exposed to high heat (without edges being held in place, ie by snaps). There was also limited room for a bolt insert in each corner of the lid and still keeping everything symmetrical.

Those were the main considerations forming the current design. I agree it could be improved, not yet sure on the best way to proceed.

garyd9, 2023-06-20:
Perhaps I should have paid closer attention to the space for the wires.  Well, bulging or not, the v6 appears to be working at least as well as the v5.  I really had no good reason for printing the new version, my v5 has been working for quite a while without issues (and no warping.)

Some other random comments:

I was very impressed with your built-in supports on the models: they worked perfectly.

The sliding cover for the cartridge is clever and installed as described in the GitHub readme.md.

Thank you for including space for 2x WAGO’s.  That made my life much easier.

I really haven’t noticed any difference in airflow between the v5 and v6, but I really have no way to measure (and it wouldn’t make sense to compare unless I could source identical fans.)

It seems like the v6 holds less carbon than the v5, but that could just be a matter of perception (because of the smaller opening to pour in carbon.)

Again, thank you sharing all your hard work.  It’s appreciated.  (This issue can be closed/resolved.)

Closed 2023-06-20.

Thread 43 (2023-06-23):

V6 Cartridge Lid Design

ptsiampas, 2023-06-23:
I love what you have done with the V6; the plenum is very nice and practical and much better than the V5.

I have been trying to fit the Jalousie, it has the flex required but because the rails its supposed to slide in are not perfect it is challenging to fit correctly; it looks great, but for ease of assembly, it's simply too hard for me to fit it as described.  I have printed it according to the settings suggested and followed the install instructions by warming up the part but no luck. I am up to my sixth print of it and still no luck.

Can you add a slid lid like the V5 for the cartridge?

Hotpocketdeath, 2023-06-25:
I concur with this.

I have been struggling to get the Jalousie slide to work, and it is way too difficult.  I've tried different materials and modified the designs a bit from the f3d files to try and put some more tolerance in and I just can't get it to work smoothly.

I'm burning through filament that I feel like this is still in prototype phase and not a final design.

I think it would be better to get rid of the bend altogether and just have a solid piece that slides straight out the side and held in by a screw.

0ndsk4, 2023-06-26:
Hi there -

Feel your frustration. The jalousie has been tested for 500+ openings, after which too much pain set in, so I know it can and does work well - for me and many others.

Hope it will become more clear in the coming weeks what filament types and slicer settings that seems to have problems with the jalousie, as this isnt an experience I wish on nevermore users. I'll leave this Issue open for others having problems to chime in.

Regarding a different lid solution - not impossible in due time to best serve users with jalousie woes, and Im happy to recieve mods which Ill upload. But currently theres little time to go back to the drawing board. As for keeping it simple, nothing is simpler (to use!) than a jalousie slider. Hopefully with more information on the matter, it can become as easy to print as to use, and we can start to agree to agree on this :)

Please state your tested filament, slicer, and in what matter the jalousie fails (bad fit, breaking, whatever) and lets see if a pattern emerges!

agravelot, 2023-06-26:
I also had a lot of trouble inserting the blind slider into the cartridge. What I had to do was clean the blind's slide path in the cartridge.

I strongly suspect this was due to my seams being positioned exactly on track. Perhaps by slightly reducing the width and/or height of the jalousie, we can increase tolerances and be more forgiving of misplaced seams and bad overhangs.

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

Adding a small filet on the Jalousie can help reducing grip into seams.

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

Printed on OrcaSlicer 1.6.3

emolitor, 2023-07-02:
I ended up solving my woes with the Jalousie door by printing it in PETG at 98% scale. With ABS it was quite hit or miss due to stiffness of eSUN ABS+ (3dqf ABS did work a bit better than eSUN ABS+) whether it would break on first insert. First attempt with PETG was very tight until I realised I needed to compensate the scale a bit due to (I supsect) less shrinkage vs the ABS printed cartridge.

I suspect that the V6 requires a relatively well tuned machine, a somewhat 'pliable' ABS and slicer settings (as noted in the docs) that generate a compliant jalousie door. With very tight tollerances the v6 design isn't very forgiving of any issues with printer tuning, material or slicer. I suspect that my setup is needs more tuning although simply changing material worked quite well for me.

w35t13, 2023-07-02:
> I ended up solving my woes with the Jalousie door by printing it in PETG at 98% scale. With ABS it was quite hit or miss due to stiffness of eSUN ABS+ (3dqf ABS did work a bit better than eSUN ABS+) whether it would break on first insert. First attempt with PETG was very tight until I realised I needed to compensate the scale a bit due to (I supsect) less shrinkage vs the ABS printed cartridge.
>
> I suspect that the V6 requires a relatively well tuned machine, a somewhat 'pliable' ABS and slicer settings (as noted in the docs) that generate a compliant jalousie door. With very tight tollerances the v6 design isn't very forgiving of any issues with printer tuning, material or slicer. I suspect that my setup is needs more tuning although simply changing material worked quite well for me.

I printed mine in esun abs+ numerous times and they all worked. even the earlier alpha's

emolitor, 2023-07-02:
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

I tried two different rolls of eSUN ABS+ on three printers (V0, Trident and X1) with only one out of six working moderately well. What slicer and what settings are you using? Obviously it works for some people and not for others so curious what is different or, as I said in my comment, if it's just down to tuning parameters. FWIW the version I printed on my Trident was the one usable one I was able to get out of eSUN ABS+.

n0ughtchill, 2023-07-02:
I was having a bit of trouble with Polylight ASA, I just shrunk the width by 1% and it's been perfect. My printer is a bit more dialed in since I printed it though so I'm not even sure if that is necessary.

0ndsk4, 2023-07-02:
Are you using ironing on top layers?

In such a thin piece like only three structural layers it might make a difference, creating an annealing effect. As I never have had a jalousie break on me, I’m trying to come up with reasons as to why.

av8er, 2023-07-03:
I also am having trouble with the door. I've tried the settings suggested with Polymaker ASA and a generic ABS. I think that the tight radius that the door has to make is part of the problem. I've noticed that once the door has the bend in it it causes friction in the straight section. I too would suggest that you make the door straight. there is no need to make the turn around the corner except for the cool factor. causes more problems than it's worth.

0ndsk4, 2023-07-03:
While I'm not opposed to a straight lid mod, the bend has a function besides looks - its what keeps the lid secure. A single axis insertion is only secure as long as its bolted or latched shut, but can otherwise slide out. Two-axis means it will always stay in place regardless of how its handled or if the cartridge is hit and falls from the magnets spilling carbon everywhere. been there, done that.

av8er, 2023-07-03:
Ok, but you could have a feature that you could press down then slide it in for the last few mm to engage the lid. Right now the sharp radius that the door has to make is unsuitable for ABS/ASA it fatigues the material and it will fail. since the "secret sauce" settings that you have for printing elude the rest of us this design is going to cause you more trouble in support than it's cool factor is worth.

emolitor, 2023-07-03:
Good question, I will have to check my slicer settings when I get back home
later in the week. You may be on to something regarding the top layer.

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

mustang5269, 2023-07-04:
I broke three of them while trying to get past the first bend until I realized that I had it upside down🤦‍♂️ for obvious reason it went right in so make sure your not making the same stupid mistake I did.

av8er, 2023-07-06:
I'm up to about 7 of these things with no success. Tried ABS, ASA & Petg all will fail. Has anyone figured out the settings necessary to get a working one of these?
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
0ndsk4, 2023-07-19:
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

The new thin jalousie option is significantly more bendable - with my abs+ filament it can be rolled into a 20mm roll, compared to 25mm using the regular version. Inspecting the rolls, the thicker roll also does not have as smooth a curve, suggesting it both bends better and smoother.

RedSinkDirty, 2023-07-22:
Print my jalaussy door in asa, it was kinda stiff to get in but it worked, I had to print 3 doors till I had the settings down to get it to print clean, just put all my speeds to 40mm/s and doubled my fan power and dropped my first layer to 10mm/s from 50.  And the in the main filter body I had to really carefully clean out the track with a razor, the track had defects at the points where the support was touching. its certainly never gonna be a one handed job on mine

emolitor, 2023-07-26:
Printed the updated door in PETG and working well, thank you.

queezz, 2023-08-11:
> I printed the revised door design in the ABS filament that previously failed. The new thinner door design works! thank you!

Same here, `[a]V6_Jalousie_Slicer_THIN[Stiff_filament][7_walls].3mf` slid right in to the case. Used Voron settings + 7 walls, printed in overture abs.

rveda, 2023-08-24:
I printed the door in PrimaSelect ABS with the suggested settings. It slid into place with some force and seemed to work. Hiwever, after a few openings it broke in half. I think I will try to reprint in PETG when I have some spare time.

I would prefer a snap-in lid or something less finicky that the slide in door.

NoahWL, 2023-09-02:
I printed the "still filament" XL jalousie in Polymaker ASA, thinking I'd have a better chance of it surviving.  I managed to get it all in with great difficulty but getting it around that first turn just required too much force and I pulled it apart.  The flexibility of the jalousie didn't seem to be the problem; the fit was just too tight in that initial path and bend.  I ran some sandpaper through that path but it didn't help much.  I then printed the jalousie at 70% Z scale, but it still required a lot of force to insert.  Finally, I lightly sanded the edges of the jalousie - the thin edges that sit in the track - and it slid right in and made it around the first bend easily.

My XL cartridge definitely warped a bit.  It stayed stuck to the bed but once it was removed (after cooling overnight) the edges of the jalousie opening pulled up toward the top of the model.  With so little rigidity around that opening I think it's fairly prone to warping, though it could just be my printer/settings.

I think making the short "insertion point" slot/track slightly wider could help, as could increasing the radius of that first turn.  On the XL cartridge especially I think increasing that turn radius would be well worth the sacrifice of carbon storage space.

0ndsk4, 2023-09-02:
>

Thank you for excellent feedback. It seems to be very common for people to pull the jalousie in, instead of pushing it. A good way of destroying it easier - it was made to push in, a mm at a time around the first bend.

Instead of telling everybody theyre wrong, I just uploaded a new thin jalousie with a pull tab. Should make insertion very easy. Any takers?

Hotpocketdeath, 2023-09-03:
So I didn't bother dealing with the Jalousie anymore and just did a redesign and made it a single solid sliding door.  Printed out just fine and the slides right in.  Tolerances came out really good first try.

Tolerances are so good in fact, I think I could remove the screw and just switch it to a detent instead.
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

0ndsk4, 2023-09-03:
Looks great, push it as a mod as a folder in the stl directory please :)

Hotpocketdeath, 2023-09-03:
> Looks great, push it as a mod as a folder in the stl directory please :)

I don't have push rights to do that.

0ndsk4, 2023-09-03:
Sorry, sent an invite now I believe. I’m not very GitHub fluent.

Hotpocketdeath, 2023-09-03:
Alright, the model has been uploaded.  Feel free to try it out.

jwyse, 2023-09-08:
@Hotpocketdeath any chance you might make and share the straight cartridge model with the same modification (for Voron V0)?

thunderkeys, 2024-02-16:
STL should be reoriented for proper printing orientation in the github - I believe it is incorrect as it sits today.

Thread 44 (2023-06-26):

Routing wires in V6?

VitalyBrusentsev, 2023-06-26:
Hi,
Could the V6 documentation be extended to include the wire routing instructions? With full size fans, it is not clear where the wires should go from the fans to the compartment. I tried to do this just snuggly on top, but it seems to not match the design intention, as it leads to the lid bulging in the middle:
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

0ndsk4, 2023-06-27:
The center wire space created by the cutout in the lid is 1.8mm in depth, afaik more than the thickness of any 5015 type wire. Increasing the depth is possible, but would increase risk of vibration movement of fan and wires and possible premature failure.

If wires lie flat, there shouldn't be any bulge in the lid. If you get a bulge, make sure that you have removed all support material on the bottom inside of the compartment, and that the wires lie flat and non-overlapping.
I added motion-GIFs to the main v6 page for full clarity.

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

Closed 2023-06-27.

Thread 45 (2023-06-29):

Missing fan hole supports in GDStime v0 model

Haxk20, 2023-06-29:
In commit https://github.com/nevermore3d/Nevermore_Micro/commit/833f6378ff79b707f6215a9e0d42d92e39b9bcc6 the fan hole supports were removed causing significant drooping of plastic on the overhangs in that area.

The other model still kept the supports so Im pretty sure this is an unwanted change and was left out by accident.

0ndsk4, 2023-07-02:
Was fixed the same day, thx!

Closed 2023-07-02.

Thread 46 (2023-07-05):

V6_Plenum[2020_extrusion].stl print issue

Marshalldog, 2023-07-05:
I love the v6 but the current print orientation for the "V6_Plenum[2020_extrusion].stl" is problematic. the print orientation of the stl positions a long, thin, edge, which makes the design highly susceptible to warping (especially considering the recommended material being abs). I tried multiple times to print it with an enclosed voron 2.4 with a chamber temp above 40 but the print consistently warped to the point of being unusable (because the magnetic warped too far away from the correct position. I'd recommend a version of the design with a print orientation like the v5 "V2_Duo_Plenum.stl" to reduce warping.

0ndsk4, 2023-07-20:
thanks for the suggestion - unfortunately, the printing direction is one of the pros of the upgrade, allowing the built in seals that prevent air leaks. it has been printed by plenty of people in regular abs, so your issue is most likely a settings/surface issue. If you want something micro sized and dont overcome these difficulties, the v5 has a different printing direction. thanks.

Closed 2023-07-20.

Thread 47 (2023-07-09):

V6 Plenum wall too thin.

Matt2916, 2023-07-09:
The wall on the upper right hand of the V6_Plenum is too thin and slices with a tiny hole.
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

0ndsk4, 2023-07-09:
Thx. This was noted on discord too. Expect a fix when back from vacationing. It’s possible to slice the wall continuously tweaking the slicer settings, which is why this wasn’t noticed earlier - however, there will always be a surface imperfection from being just a single wall. This will be updated.

Matt2916, 2023-07-09:
My v5 works still fine, so I'll wait for the update - have a great vacation!

0ndsk4, 2023-07-20:
issue has now been fixed in alla files, thanks!

Closed 2023-07-20.

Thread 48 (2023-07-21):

V6_Plenum[2020_extrusion] fan clips midair

AlbinoDeer, 2023-07-21:
Noticed this after my print started to fail, but the two pieces that print alongside the main body to hold the fans in are midair. Just looking at the other STLs they are flat on the bed.

0ndsk4, 2023-07-22:
thanks, fixed now!

Closed 2023-07-22.

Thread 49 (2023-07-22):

the poke yoke tongue on the v6 cartridge doesn't actually stop reversal on the straight cart.

RedSinkDirty, 2023-07-22:
(sorry if this is a overloaded issue Its kind of just misc feedback and soft issues. Feel free to just bonk and close it)

Maybe its not meant to stop the filter from being put on the other way around, but the tongue on the filter that pokes into the main body doesn't do anything on the straight cartridge when flipped around. It looks like I have the filter on backwards by the tongue but this is actually the way I would want the filter for my trident,
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

and then for the trident mount am I supposed to put the nevermore on the back wall or the side, a little more instruction on mounting might be nice, just saying it wasn't clear, Ill figure it out or make my own mount. Id guess more mounting pictures/directions are planned. If I had noticed before I printed it I probably would have flipped the text for the way I'm mounting it, lol youre using the v6 Im on 9 delta. I also didn't print the 2020 mount because I didn't read but also because it was labeled optional in the folder. Where's the other heatset insert go?
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

and and, I ended up cutting a lot of the grating out of the top of the straight cartridge, the profile(default prusa voron v2) I had printed it with had 3mm mini travel after retract and with my abs not being extremely dry, every hole was pretty much crossed out with stringing. it'll be fine at least with your pellets nothing seem to fall out. Probably would have printed a version with the more open grate anyway since its gonna be standing up in my trident
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
or maybe its just that prusa 2.6 wants to do a line of bridges before perimeters but it starts and stops extrusion, and the wall drags plastic out of the nozzle so its not primed to start and stop like it tries to. and the it came back later to finish some of them, I wonder if a small  gap below the first layer of the cross grating would turn it into only 5 continues bridges, maybe I just have a setting funky, I messed around a little but it didn't seem to want to act differently.
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

I forgot to take pictures but winsin fans worked fine I just had to trim off two of the closure snaps for them to sit well, the spring clips hold them well.
The 3x jst mount seemed to work well, I plugged in the connections and then cut and resoldered the wires to the fans so there wasn't much extra wire.

RedSinkDirty, 2023-07-22:
doh the prusa screen shot is the other side of grating. eh that side was pretty messy top but better

RedSinkDirty, 2023-07-23:
Is this how the trident mount was intended? And I had to plug the unused mounting hole, soooo much air was coming out of it.
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

0ndsk4, 2023-07-23:
I believe the trident mount is for mounting it back+side under the bed at one or both sides of the T-shaped extrusion.

Intention of the “key” on the cartridge was to ensure perfect attachment when you can’t see the plenum (ie under the bed of a v2). Up side down attachment is not an issue then.

RedSinkDirty, 2023-07-23:
> I believe the trident mount is for mounting it back+side under the bed at one or both sides of the T-shaped extrusion.

I held it up on the t frame of the bed it didn't really seem to make sense anywhere on a 300 size because it doesn't reach past the edge of the bed.  on a 250 I guess that would make sense. and then on the back wall along the floor it cant reach past the z motor mount "plate" and the outer corner extrusion has wires running there.  so the place in the second picture wasn't really a option.

I'm happy with where I have it now though. I think the air circulation path will be good here.

Closed 2023-07-24.

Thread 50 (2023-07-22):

Remove fan clips from v6 Plenum stl and post separately

gx1400, 2023-07-22:
Tried to print my v6 plenum last night but due to closed issue #48, my clips were both failed

https://github.com/nevermore3d/Nevermore_Micro/issues/48

Although i do need to reprint the plenum after it split snapping in the lid, printing those clips separately (and being able to move them around on the print bed) would be helpful

0ndsk4, 2023-07-22:
STL files containing different bodies can easily be split via “Split To Objects” in PS/SS or mesh tools in cura.

https://help.prusa3d.com/article/split-to-objects-parts_1751

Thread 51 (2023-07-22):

V6 Jalousie instructions unclear

gx1400, 2023-07-22:
"Also 90 degrees infill angle, so the 3rd layer is printed in this orientation."

An image of the slicer in the correct, and possibly incorrect configuration, would be helpful here

I am unsure what this orientation is referring to

SapuSeven, 2023-09-12:
In SuperSlicer/PrusaSlicer, under "Print Settings" -> "Infill" set "Fill Angle" to 90deg (default: 45deg)

HitLuca, 2024-01-16:
Same here, what is *this* orientation referring to? I think there's a missing explanatory image

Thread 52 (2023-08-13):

Issue when mounting with kinematic supports

theodiem, 2023-08-13:
Hello,
I've noticed an issue when mounting nevermore V6 in a Voron V2 with the kinematic bed mounts.
The mounts are slightly larger than the 2020 leading to issues mounting it.
I don't know if it would be possible to increase the chanfer on the upper corder a little bit to accomodate it without creating an issue with airflow/fans.
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

ndanyluk, 2024-03-08:
+1 for this issue on my V2 as well.  I'll take a look at the cad and see if a cutout there would break things

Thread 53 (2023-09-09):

V6 plenum for V0 with Winsinn fans

jwyse, 2023-09-09:
**My Winsinn blowers don't fit properly in the "Delta_GDStime_Winsinn" plenum, but they fit well in the "Sunon_Honeybadger" plenum.**

I have Winsinn 5015 blowers (just purchased from Amazon US), so I printed the corresponding plenum for my Voron 0, `V6/v0/v0_Plenum_Delta_GDStime_Winsinn.stl`.  The blowers fit very poorly due to the clips that hold the blower shell together and insufficient clearance in the plenum.  The only difference I can see between the two plenum models (I only looked at the v0-specific variations) is the clearance for the blower clips.  I did a quick draft-quality PLA print of the other plenum model (`V6/v0/v0_Plenum_Sunon_Honeybadger.stl`) just out of curiosity, and the Winsinn blowers fit in that one much better.

Has anyone else experienced this?  Maybe the Winsinn product spec changed, or perhaps the Nevermore models/documentation could be improved by mentioning possible variations in the wild.

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

CRTified, 2024-01-14:
Still bootstrapping ABS/ASA-printing, so I've printed the `V6/v0/v0_Plenum_Delta_GDStime_Winsinn.stl` out of PETG. Can confirm that it's not really a good fit.

What file did you end up using?

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

CRTified, 2024-01-15:
Being a bit more generous while removing the support made it fit for me. Guess I'll give it a shot :)

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

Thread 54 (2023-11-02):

CAD files for XL cartridge

Jessi810, 2023-11-02:
Can't find the CAD files for XL variant. I would like to modify it a bit before printing.

0ndsk4, 2023-11-03:
added this

Closed 2023-11-03.

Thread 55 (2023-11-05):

XL cartridge and jalousie not fit

Jessi810, 2023-11-05:
The jalousie is 0.2mm thicker than the cartridge's jalousie slider (not sure what to name it, image below for reference).

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

0ndsk4, 2023-11-05:
Yeah, true. Tolerance seems too little. I might have too much squish prototyping :)

Try the two thin/stiff filament jalousie variations if you have a hard time fitting it, They are 0.2mm thinner. Will likely update the cartridge file with a bit more wiggle room. Thanks.

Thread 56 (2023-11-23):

V6 half

padok, 2023-11-23:
Hi,

I was wondering if anyone is interested in a V6 "half" version.

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

I just threw this together with "split body", I would love some feedback first and maybe the original Fusion? files, for the final version.

I imagine it could go on the left and right side of the bed of my V2.4, so that the airflow would be stronger in the same up direction, which I can't quite achieve with a fan mod like the one from [Ellis](https://github.com/VoronDesign/VoronUsers/tree/master/printer_mods/Ellis/Bed_Fans).

At the moment I'm planning to use it without filter bags, but theoretically a single bag should fit, right?

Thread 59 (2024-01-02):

Unable to print V6 Cartridge built-in support

Lee-Arthur, 2024-01-02:
V6 Cartridge 90 degree:
Prusa Slicer:
Voron V2.4

Prusa Slicer removes the large built-in support for the sliding door presumably because the slicer perceives inadequate attach points for the support.  Modifying the STL to add a random square object to the support object does force Prusa Slicer to print with the support in place, however, the print still fails when printing the support portion because of inadequate attachment between support and structure.

Unable to print object.

btthrt, 2024-02-27:
Had no problems with prusa slicer. Probably something is messed up with your config.

kitkat0981, 2024-08-12:
I’m having the same issue with orca slicer with asa. The panel keeps warpin
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

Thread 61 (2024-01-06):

Its not made clear how long the carbon that is resold lasts

hYdos, 2024-01-06:

0ndsk4, 2024-01-06:
Hi!

The original manufacturer guarantees two years. Worst case, it’s six months old by the time it gets to vendors. Most vendors restock with 1-3 months interval, but say a worst case here would be six months as well, it’s still perfectly good for use a year after purchase (and likely longer as it’s quite optimally stored in a light vacuum compression with very few factors that can deplete or damage the micro-porosity).

But you can assume Nevermore carbon is good for at least a year, and likely longer.

hYdos, 2024-01-06:
thanks for the info

Closed 2024-01-06.

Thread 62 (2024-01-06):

API klipper for changing carbon after notofication?

mwalter665, 2024-01-06:
Hello,

i have already several API endpoints from klipper, so that I get infos to my homeassistant. For example the whatsapp message when a print is ready, or switching Power of when the temp of the head is under 40°C.

Now I thougt that I can get the statistics from klipper too and every x hours of printing i get a notification to change the carbon in the box.

The YAML and sensors  with calculating in homeassistant is not the problem, but I couldn´t find an endpoint for getting the values, which I can see on the history page of mainsailos. Has anyone maybe an idea? Or how do you bei informed if the the  50 hours are gone since last change?

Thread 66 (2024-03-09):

[CAD] Step file upload possible?

ndanyluk, 2024-03-09:
Hi! I love my Nevermore Micro V4 & V5 and was about to print a V6 for my V2, but ran across #52

I was going to look at the CAD to try and modify the filter cartridge (the plenum should be fine), but realized that it's only available as an f3d file. Since I use OnShape this was a bit problematic.  Could you possibly upload the CAD as a STEP since it's a bit more portable for those who don't use F360?

BenJBachler, 2024-04-07:
I would also like the step files for the parts.

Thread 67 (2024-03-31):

Wraping

mazimazurski, 2024-03-31:
Hi there!
There is a high chance that parts will wrap during printing.
My 3 attemps: in the photos, the last one with glue and brim but also not perfect.
My setup :voron 2.4 with chamber, abs Fiberlogy
I know that not only I had a problems with printing these parts.
There is no problem with wraping of v6_Cartridge_90deg - because the last layer is most critical and is finnally flat.
Do You have some print advice ?
Soome solution is to turn upside down the part V6_Plenum for printing, then last layar is also for sure flat.
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

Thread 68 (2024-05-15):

Wago connector clarifications

Tarakesh83, 2024-05-15:
It should be noted in the BOM that for the Wago connector the part number 221-422 or 221-412 is needed.
The Wago 221 Series has 2 different sizes. The 221-4 and  the 221-6.
221-6 is bigger and does not fit into the mounting  space.

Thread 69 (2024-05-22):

V6 XL HEPA cartridge -- lower about 1 cm?

staspika, 2024-05-22:
If only the XL HEPA cartridge were about 1 cm lower, the Voron 0 print head would perfectly clear it 🤔 Here shown with a Dragon Burner print head, but it is about the same height as the stock head. Is there any reasons why it shouldn't?
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
On the right side (the A motor side) it might still collide with Kirigami mod bed, if not pulled far enough towards the front, but on the left side (the B motor side) it otherwise seem to be the perfect fit.

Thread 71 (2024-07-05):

Please consider this alternative to the jalousi

matthew-humphrey, 2024-07-05:
I really love the improvements in the Nevermore Micro v6 - everything but the jalousi. I have a well-tuned printer and ASA print profile, and so I had no problems printing it and installing. However, the design seemed fragile, so I spent some time opening and closing it a few times to see how robust it was. As expected, it broke.

I totally get the design to have a toolless design. Maybe a snap-fit lid would work?

I also wanted to pass along this design, which, while not toolless, is very robust and works for both the 90 degree and straight cartridges:

https://www.printables.com/model/514532-nevermore-v6-carbon-filter-easy-lid-remix/

Thanks very much for designing this wonderful add-on - I use it in all my printers.

thijstriemstra, 2024-07-11:
thanks for the suggestion, I'm also going for this alternative.

YoungHillionaire, 2024-07-13:
thank you.
i will try printing this once i install my xol toolhead

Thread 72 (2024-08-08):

Why push air thrue filter?

Shedatheds, 2024-08-08:
Why is the filter not on intake side of the fan at V6? It would be more efficient to have the filter on intake side!

0ndsk4, 2024-08-09:
Originally due to the space constraints under the bed of the voron v2.4. And while a push configuration can be more efficient, it’s also true that’s not the case with a highly restrictive filter in front of fast airflow.

It would likely take a thicker version to achieve the intake space needed for rotated fans. Then again, it wouldn’t come near a nevermore mini in airflow, and a mini is not that much thicker… feel free to mod the micro tho :)

Closed 2024-08-09.

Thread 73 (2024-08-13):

cannot print the V6 Plenum 2020 - no layers?

kitkat0981, 2024-08-13:
im getting an error in Orca Slicer that i have never seen before.

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

How can I fixe this?

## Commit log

2021-10-06 Move to new repo
    [1,8_Frame_Connector.stl, BASES_V1.stl, BASE_V0_1515.stl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]
2021-10-08 Rename 1 space in 'V5 Duo' to 'V5_Duo'
    [1,8_Frame_Connector.stl, Duo_Cartridge_LID.stl, Duo_Plenum_RC7_DELTA.stl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]
2021-10-26 Cleanup Files; Update some Models (#1)
    * Clearify V4 and V5 variants
    * Move V5 mods to Mods/; Rename Mods Folders
    * Move F3d files to respected directories
    [Naked_RLF-35_with_Wago_Triples_Mk1.stl, Nevermore-RLF35_LID_v01_by_Dave.stl, Nevermore_Micro v4.f3d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]
2021-11-20 Update readme (#2)
    Adding slightly increased clarity about VOCs and grammar adjustments. The term VOCs is thrown around a lot (especially in Discord) with the intent of harmful chemicals but VOCs are also the harmless chemicals such as typical odors like farts. I make the mistake myself a lot by using VOCs to refer to the harmful components while forgetting of the harmless ones. This was especially apparent in our discussions on VOC sensors.
2021-12-19 Update README.md
    warning about not making a PID tune
2022-02-08 Add files via upload
    faulty fillet in magnet hole removed
2022-03-27 Update README.md
    more fan info under the other headline
2022-05-19 Add files via upload
    Removed faulty magnet fillet
    [Duo_XL_Cartridge.3mf]
2022-07-09 Update README.md (#12)
    Updated the BOM for more detail
2022-09-11 Added STL for Duo_XL_Cartridge and removed the corresponding 3mf file. (#14)
    [Duo_XL_Cartridge.3mf]
2022-11-13 Add slide-in magnet mod. (#16)
    * Add slide-in magnet mod.
    * Fix orientation of lid STL
    * Update README.md
    * Add backmounted plenum
    Based on the one from @mvieleers
    [Duo_Plenum.step, Duo_Plenum.stl, Duo_Plenum_Lid.step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]
2023-03-29 Add files via upload
    added the fusion file for the v0 plenum
    [V0_Plenum.f3d]
2023-04-12 bucknova fixed the strange artifacts
    [Regular_Cartridge(contributed_by_Bucknova).3mf, Regular_Cartridge_Lid(contributed_by_Bucknova).3mf, XL_Cartridge(contributed_by_Bucknova).3mf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]
2023-04-12 accidental delete
    [V2_Duo_Plenum_LID.stl]
2023-04-12 Cartridges with artifact fixes by bucknova
2023-05-18 BOM4/5: Fix "0.5mm" inserts, and specify ⌀/height on magnets (#31)
    * BOM4/5: Fix "0.5mm" inserts, and specify ⌀/height on magnets
    * Remove "cylindrical" from magnet specs, 6x3 is more "round".
    * Fix number of heat inserts for V5
    Copy from PR #32 by MarcelRobitaille
2023-06-03 Beta Plenum CAD files
    Note that this plenum has back mounting slot suitable for a v0 1515 extrusion.
    [V6_90_Degree_Cartridge.f3d, V6_PLENUM.f3d]
2023-06-04 faulty top bridging corrected,
    previous version was somehow 0.4 degrees off causing the bridging to fail
    [V6_PLENUM.f3d]
2023-06-04 a straight flow cartridge for the v6 system
    ported from v5
2023-06-04 add Trident frame mount (#36)
    * Add files via upload
    Trident rear mount for corner extrusion. use in conjunction with 1.8 frame mount
    * Delete v6_trident_rear_mount.stl
    wrong orientation
    * Add files via upload
    corrected orientation
    [v6_trident_rear_mount.stl]
2023-06-04 a straight cartridge for v6
    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
    [v6_Cartridge_Straight.stl]
2023-06-04 connect v6 to an extrusion!
    [1515_Frame_Connector.stl, 2020_Frame_Connector.stl]
2023-06-04 plenum with 2020 extrusion back mounting
    [V6_PLENUM_2020_Extrusion.f3d]
2023-06-04 plenum with 2020 extrusion back mounting
    can go on the panel of a trident for instance
2023-06-05 support heights adjusted fit exactly 0.2 layers
    now supports will work equally well on any slicer.
    [V6_90_Degree_Cartridge.f3d]
2023-06-05 support heights adjusted fit exactly 0.2 layers
    Now supports will not slicer-dependently fail. Supports has also been connected at the bottom, and a few more contact points have been added to decrease risk of breaking during printing.
    [v6_Cartridge_90deg.stl, v6_Cartridge_Straight.stl]
2023-06-06 Update README.md
    BOM and instructions
2023-06-08 improved bridgning+support
    top side bridging simplified, should hopefully now work with slightly larger nozzles too.
    added lateral support adhesion points, should hopefully help avoid the support warping and coming loose when printing in regular abs/asa
    [V6_90_Degree_Cartridge.f3d]
2023-06-08 improved bridging and support
    better top side bridgning, added lateral adhesion points for the support so is hopefully cant warp when printing with regular abs/asa
    [v6_Cartridge_90deg.stl]
2023-06-08 improved bridging and support
    [V6_90_Degree_Cartridge.f3d]
2023-06-08 improved bridging and support
    hopefully avoids support warping when printing in regular abs/asa with improved lateral adhesion points. better top side bridging, hopefully works better with slightly larger nozzles than 0.4
    [v6_Cartridge_Straight.stl]
2023-06-09 Plenum Files for Sunon and Honeybadger fans
    Intake hole placement differs and is offset. These files will fit Sunon and Honeybadger fans better
    [V6_PLENUM_1515_SUNON_HONEYBADGER.f3d, V6_PLENUM_2020_SUNON_HONEYBADGER.f3d]
2023-06-11 printability fixes
    slider path optimized for layer height, removed unsupported areas for increased printability
    [v6_Cartridge_90deg.stl]
2023-06-11 chamfered jalousie
    has a 45 degree chamfer which lessens the risk of getting stuck on the first bend. for users who have experienced jalousie insertion failure
2023-06-11 less-insertion-stuck-jalousie
    chamfered insertion angle giving this version less risk of getting stuck upon first insertion. to try for users who are having trouble with the regular jalousie
2023-06-13 bends better for easier insert
    should also print with less fusing due to increased tolerances
    [[a]V6_Jalousie_Slicer.stl]
2023-06-13 the jalousie
    if anyone want to play around with it
    [Jalousie_ v2.f3d]
2023-06-13 text reorientation
    courtesy of @livinhack, as the back side text was upside down when mounted in the bottom of a v0
    [V0_90_Degree_Cartridge_V6.f3d, V0_PLENUM_1515_Extrusion_V6.f3d, V0_PLENUM_1515_SUNON_HONEYBADGER_V6.f3d]
2023-06-13 courtesy of @livinhack
    text orientation
    [v0_Plenum_Delta_GDStime_Winsinn.stl]
2023-06-13 printability update
2023-06-13 @livinhack plus latest printabilaty fixes
    [V0_90_Degree_Cartridge_V6.f3d, v0_90deg_Cartridge.stl, v0_Straight_Cartridge.stl]
2023-06-16 extrusion holes were 2.5mm off
    [V6_PLENUM_2020_Extrusion.f3d]
2023-06-16 old was 1515 side holes, not 2020. now fixed
2023-06-21 fixed v2.4 mounting holes issue
2023-06-28 magnet holes offset fix
    magnet holes offset fix
    [V6_PLENUM_1515_SUNON_HONEYBADGER.f3d, V6_PLENUM_2020_SUNON_HONEYBADGER.f3d]
2023-06-28 magnet hole offset fix
    magnet hole offset fix
2023-06-29 magnet offset fix
    magnet offset fix
    [V0_PLENUM_1515_Extrusion_V6.f3d, V0_PLENUM_1515_SUNON_HONEYBADGER_V6.f3d]
2023-07-18 33% thinner, bends better
    [[a]V6_Jalousie_Slicer_THIN[Stiff_filament][7_walls].3mf]
2023-07-19 Thin wall bug removed
    Will print with no surface artifacts and two walls with 0.4mm layer width
    [V0_PLENUM_1515_Extrusion_V6.f3d, V0_PLENUM_1515_SUNON_HONEYBADGER_V6.f3d]
2023-07-19 thin wall fix
    [V6_PLENUM_1515_SUNON_HONEYBADGER.f3d, V6_PLENUM_2020_SUNON_HONEYBADGER.f3d]
2023-07-19 thin wall fix
    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
    [V6_PLENUM_1515_Extrusion.f3d, V6_PLENUM_2020_Extrusion.f3d]
2023-07-20 v6 cartridge with 3X the carbon space plus HEPA
    [1_XL_Cartridge.stl, 2_XL_HEPA_Container[reg].stl, 2_XL_HEPA_Container[small_hex].stl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]
2023-07-22 fixed floating clamps
2023-07-22 filter link
2023-09-02 pull tab jalousie for easier insertion
    [[a]V6_Jalousie_Slicer[TAB][THIN].stl]
2023-09-02 pulltab for easier insertion
    [3_XL_Jalousie[THIN_with_PULLTAB].stl]
2023-10-23 increased depth for pre filter, added tab slot
    [2_XL_HEPA_Container[reg].stl]
2023-12-18 Alternate sliding door mod repairs (#57)
    * orientation fix
    * Planer cut for fixed 1st layer
    [Sliding_door.stl, v6_Cartridge_90deg_Sliding_Door_Mod.stl]
2025-01-01 simplify V6 BOM (#74)
